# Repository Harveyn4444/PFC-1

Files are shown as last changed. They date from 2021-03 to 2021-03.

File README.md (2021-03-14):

# PFC-1
Hardware and software for the Team Peryton Flight Computer v1

Currently a work in progress

The flight computer is designed around an ATMEGA328 and provides live telemetry and onboard data storage.
GPS, BME280, MPU9250, SGP30, microSD data storage, LoRa comms to a ground-station.

This is designed to fit comfortably in model rockets of 30mm internal diameter.

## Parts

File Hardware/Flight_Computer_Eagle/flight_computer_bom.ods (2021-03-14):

Part | Value | Device | RS / eBay | Units
C1 | 100n | C-EUC0603 | 264-4630 | 25
C3 | 100n | C-EUC0603 | '’
C4 | 100n | C-EUC0603 | '’
C5 | 10u | CPOL-EUSMCA | 538-2278 | 10
C6 | 10u | CPOL-EUSMCA | '’
C20 | 100n | C-EUC0603 | '’
C25 | 100n | C-EUC0603 | '’
D1 | 1A/40V/500mV | BAS40 | in stock
GPS_ANT | U.FL | U.FL
GPS_FIX |  | LEDCHIPLED_0603
J1 |  | JST_2MM_MALE
L1 | 27u | L-EUL1812
LORA_ANT | SMA_EDGE | SMA_EDGE
PROG_HEADER |  | CONN_06FEMALE_LOCK
R1 | 200 | R-EU_R0603
R2 | 10k | R-EU_R0603
R19 | 10k | R-EU_R0603
R20 | 10k | R-EU_R0603
R23 | 1k | R-EU_R0603
R24 | 1k | R-EU_R0603
R25 | 22 | R-EU_R0603
SD | TF-HOLDER | TF-HOLDER
TEST_LED |  | LEDCHIPLED_0603
U$1 | SMD_JUMPER | SMD_JUMPER
U$2 | MPU9250_BB | MPU9250_BB
U$3 | RFM96W | RFM96W
U$4 | 24AA32A | 24AA32A
U$5 | TINY_CELL_GPS | TINY_CELL_GPS
U$6 | NEO-6M_GPS | NEO-6M_GPS
U$7 | BME280 | BME280
U$8 | SGP30_BREAKOUT | SGP30_BREAKOUT
U1 | ATMEGA328P_TQFP | ATMEGA328P_TQFP
U3 |  | V_REG_LM1117SOT223
Y1 | 8MHz | RESONATOR-8MHZSMD_3.2X1.3

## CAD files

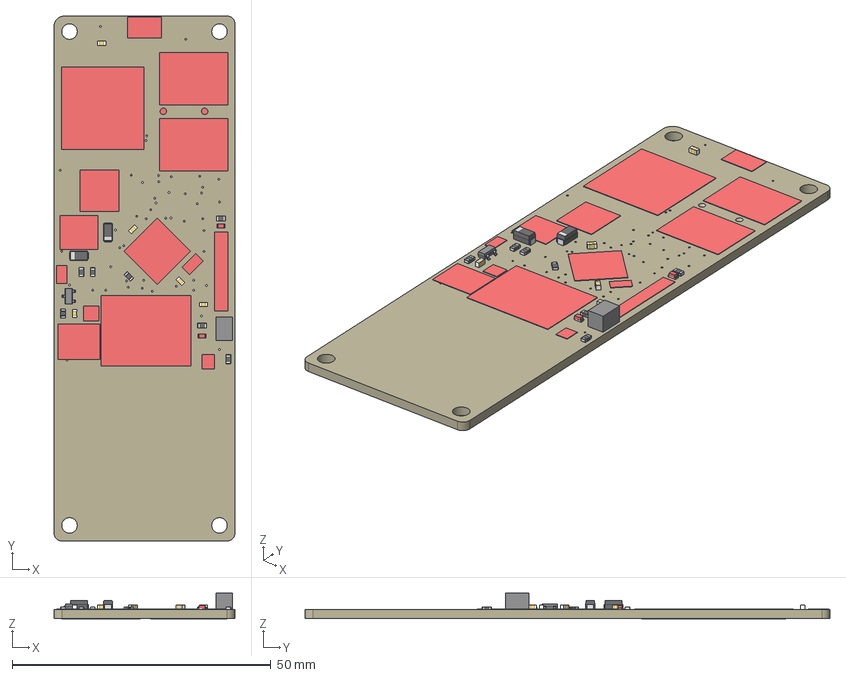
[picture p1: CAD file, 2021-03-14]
Hardware/flight_computer.step
35.0 x 101.5 x 4.97 mm
Board
100n x 5
10u x 2
1A/40V/500mV
CHIPLED_0603 x 2
JST-2-SMD
27u
1X06_FEMALE_LOCK.010
RFM96W
24AA32A
TINY_CELL_GPS
NEO-6M_GPS
SGP30_BREAKOUT x 2
ATMEGA328P_TQFP
SOT223
TF-HOLDER
8MHz
SMD_JUMPER
MPU9250_BB
U.FL
SMA_EDGE

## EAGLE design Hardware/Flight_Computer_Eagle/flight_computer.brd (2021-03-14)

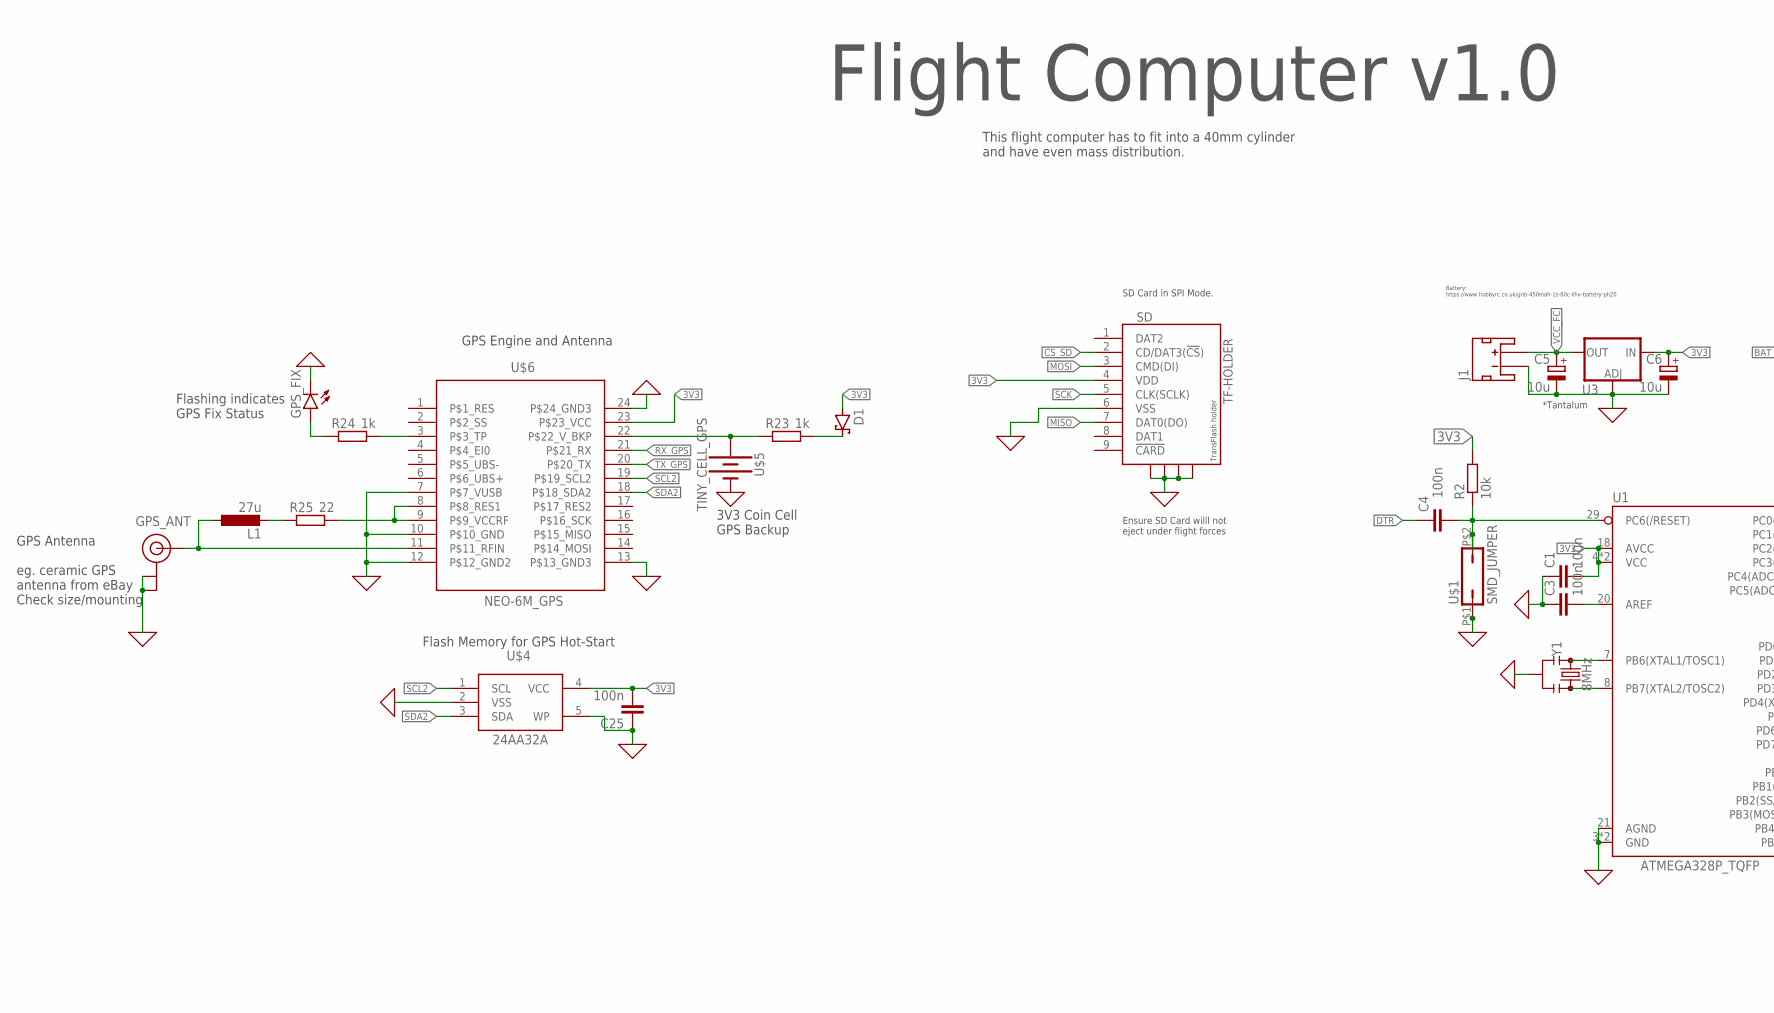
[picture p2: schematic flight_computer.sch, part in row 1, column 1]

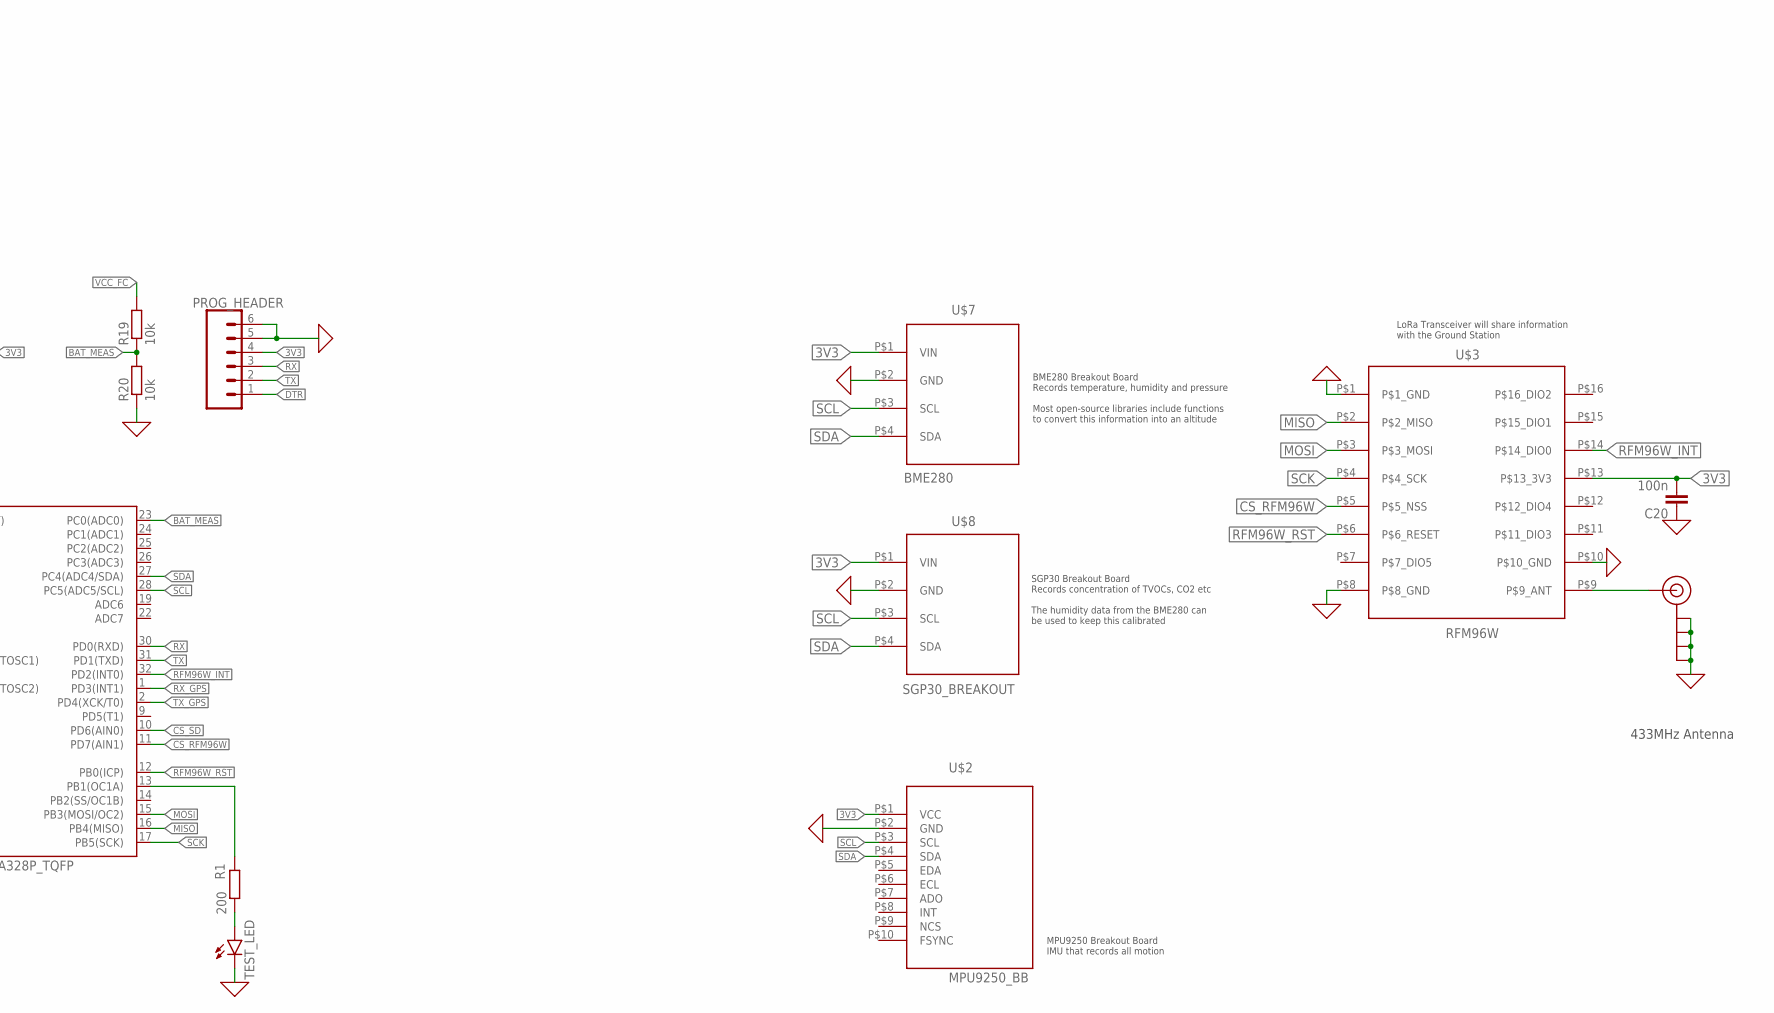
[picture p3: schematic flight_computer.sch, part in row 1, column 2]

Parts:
C1, C3, C4, C20, C25: 100n; C0603
C5, C6: 10u; SMC_A
D1: 1A/40V/500mV; SOT23
GPS_ANT: U.FL
GPS_FIX: LEDCHIPLED_0603; CHIPLED_0603
J1: JST_2MM_MALE; JST-2-SMD
L1: 27u; L1812
LORA_ANT: SMA_EDGE; SMA-EDGE
PROG_HEADER: CONN_06FEMALE_LOCK; 1X06_FEMALE_LOCK.010
R1: 200; R0603
R2, R19, R20: 10k; R0603
R23, R24: 1k; R0603
R25: 22; R0603
SD: TF-HOLDER; TF-PULL
TEST_LED: LEDCHIPLED_0603; CHIPLED_0603
U1: ATMEGA328P_TQFP; TQFP32-08
U3: V_REG_LM1117SOT223; SOT223
U$1: SMD_JUMPER
U$2: MPU9250_BB
U$3: RFM96W
U$4: 24AA32A; SOT23-5L
U$5: TINY_CELL_GPS; TINY_SMD_CELL
U$6: NEO-6M_GPS; NEO-M9N/M8T/M8U
U$7: BME280; BME280_BREAKOUT
U$8: SGP30_BREAKOUT; BME280_BREAKOUT
Y1: 8MHz; RESONATOR-SMD-3.2X1.3

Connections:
0: C1.1, C3.1, C5.-, C6.-, C20.1, C25.1, GPS_ANT.1 (GND), GPS_ANT.2 (GND), GPS_FIX.C, J1.1 (-), LORA_ANT.GND@0 (GND), LORA_ANT.GND@1 (GND), LORA_ANT.GND@2 (GND), LORA_ANT.GND@3 (GND), PROG_HEADER.5, PROG_HEADER.6, R20.1, SD.6 (VSS), SD.S1, SD.S2, SD.S3, SD.S4, TEST_LED.C, U1.3 (GND), U1.5 (GND), U1.21 (AGND), U3.1 (ADJ), U$1.P$1 (1), U$2.P$2 (GND), U$3.P$1 (P$1_GND), U$3.P$8 (P$8_GND), U$3.P$10 (P$10_GND), U$4.2 (VSS), U$4.5 (WP), U$5.P$1 (-), U$6.7 (P$7_VUSB), U$6.10 (P$10_GND), U$6.12 (P$12_GND2), U$6.13 (P$13_GND3), U$6.24 (P$24_GND3), U$7.P$2 (GND), U$8.P$2 (GND), Y1.2
3V3: C1.2, C6.+, C20.2, C25.2, D1.1 (A), PROG_HEADER.4, R2.2, SD.4 (VDD), U1.4 (VCC), U1.6 (VCC), U1.18 (AVCC), U3.3 (IN), U$2.P$1 (VCC), U$3.P$13 (P$13_3V3), U$4.4 (VCC), U$6.23 (P$23_VCC), U$7.P$1 (VIN), U$8.P$1 (VIN)
BAT_MEAS: R19.1, R20.2, U1.23 (PC0(ADC0))
CS_RFM96W: U1.11 (PD7(AIN1)), U$3.P$5 (P$5_NSS)
CS_SD: SD.2 (CD/DAT3(!CS!)), U1.10 (PD6(AIN0))
DTR: C4.1, PROG_HEADER.1
MISO: SD.7 (DAT0(DO)), U1.16 (PB4(MISO)), U$3.P$2 (P$2_MISO)
MOSI: SD.3 (CMD(DI)), U1.15 (PB3(MOSI/OC2)), U$3.P$3 (P$3_MOSI)
unnamed: U1.7 (PB6(XTAL1/TOSC1)), Y1.1
unnamed: U1.8 (PB7(XTAL2/TOSC2)), Y1.3
unnamed: R1.1, U1.13 (PB1(OC1A))
unnamed: R1.2, TEST_LED.A
unnamed: C4.2, R2.1, U1.29 (PC6(/RESET)), U$1.P$2 (2)
unnamed: C3.2, U1.20 (AREF)
unnamed: LORA_ANT.SIG (SIGNAL), U$3.P$9 (P$9_ANT)
unnamed: R23.1, U$5.P$2 (+), U$6.22 (P$22_V_BKP)
unnamed: D1.3 (C), R23.2
unnamed: R24.2, U$6.3 (P$3_TP)
unnamed: GPS_FIX.A, R24.1
unnamed: R25.2, U$6.8 (P$8_RES1), U$6.9 (P$9_VCCRF)
unnamed: GPS_ANT.FEED (SIGNAL), L1.1, U$6.11 (P$11_RFIN)
unnamed: L1.2, R25.1
RFM96W_INT: U1.32 (PD2(INT0)), U$3.P$14 (P$14_DIO0)
RFM96W_RST: U1.12 (PB0(ICP)), U$3.P$6 (P$6_RESET)
RX: PROG_HEADER.3, U1.30 (PD0(RXD))
RX_GPS: U1.1 (PD3(INT1)), U$6.21 (P$21_RX)
SCK: SD.5 (CLK(SCLK)), U1.17 (PB5(SCK)), U$3.P$4 (P$4_SCK)
SCL: U1.28 (PC5(ADC5/SCL)), U$2.P$3 (SCL), U$7.P$3 (SCL), U$8.P$3 (SCL)
SCL2: U$4.1 (SCL), U$6.19 (P$19_SCL2)
SDA: U1.27 (PC4(ADC4/SDA)), U$2.P$4 (SDA), U$7.P$4 (SDA), U$8.P$4 (SDA)
SDA2: U$4.3 (SDA), U$6.18 (P$18_SDA2)
TX: PROG_HEADER.2, U1.31 (PD1(TXD))
TX_GPS: U1.2 (PD4(XCK/T0)), U$6.20 (P$20_TX)
VCC_FC: C5.+, J1.2 (+), R19.2, U3.2 (OUT), U3.4 (OUT)

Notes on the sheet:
*Tantalum
433MHz Antenna
Ensure SD Card willl not eject under flight forces
Flash Memory for GPS Hot-Start
GPS Engine and Antenna
Flashing indicates GPS Fix Status
3V3 Coin Cell GPS Backup
GPS Antenna eg. ceramic GPS antenna from eBay Check size/mounting
Battery: https://www.hobbyrc.co.uk/gnb-450mah-1s-80c-lihv-battery-ph20
SD Card in SPI Mode.
BME280 Breakout Board Records temperature, humidity and pressure Most open-source libraries include functions to convert this information into an altitude
SGP30 Breakout Board Records concentration of TVOCs, CO2 etc The humidity data from the BME280 can be used to keep this calibrated
LoRa Transceiver will share information with the Ground Station
This flight computer has to fit into a 40mm cylinder and have even mass distribution.
Flight Computer v1.0
MPU9250 Breakout Board IMU that records all motion

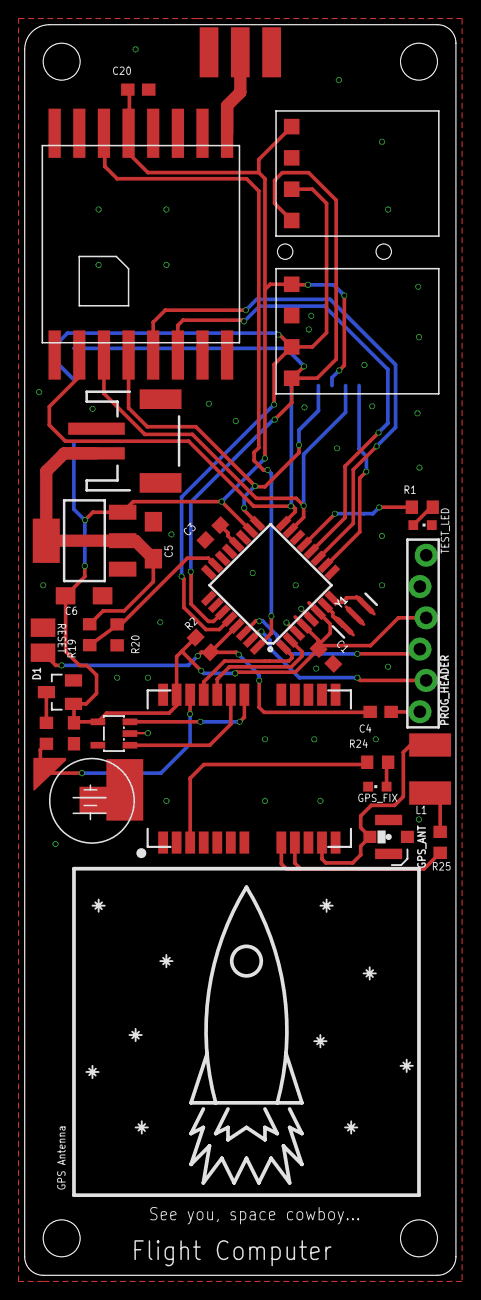
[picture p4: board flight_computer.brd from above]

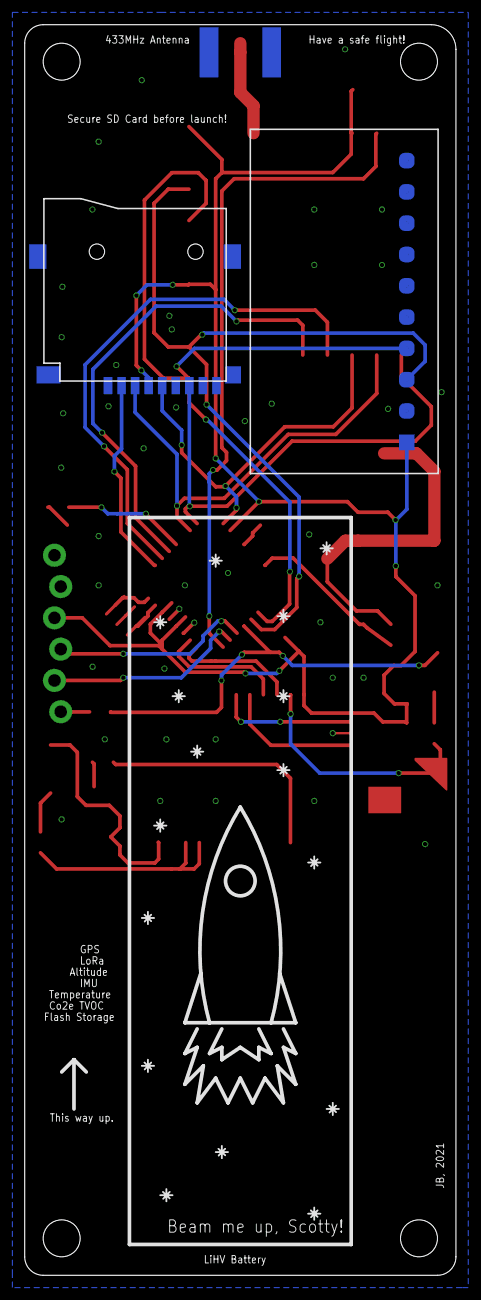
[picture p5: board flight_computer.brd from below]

Board: 2 copper layers, 35.0 x 101.5 mm, 34 parts (2 on the bottom side), 34 nets.

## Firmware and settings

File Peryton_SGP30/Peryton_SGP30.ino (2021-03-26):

#include <Wire.h>
#include "Adafruit_SGP30.h"

Adafruit_SGP30 sgp;

uint32_t getAbsoluteHumidity(float temperature, float humidity) {
    // approximation formula from Sensirion SGP30 Driver Integration chapter 3.15
    const float absoluteHumidity = 216.7f * ((humidity / 100.0f) * 6.112f * exp((17.62f * temperature) / (243.12f + temperature)) / (273.15f + temperature)); // [g/m^3]
    const uint32_t absoluteHumidityScaled = static_cast<uint32_t>(1000.0f * absoluteHumidity); // [mg/m^3]
    return absoluteHumidityScaled;
}

int counter = 0;
float TVOC;
float eCO2;
float H2;
float Ethanol;


void setup() {
 Serial.begin(115200);
 delay(500);
 Serial.println("SGP30 test");

  if (! sgp.begin()){
    Serial.println("Sensor not found");
    while (1);
  }
  //This outputs the sensors chips unique serial number, not too sure if necessary
  Serial.print("Found SGP30 serial #");
  Serial.print(sgp.serialnumber[0], HEX);
  Serial.print(sgp.serialnumber[1], HEX);
  Serial.println(sgp.serialnumber[2], HEX);

   if (! sgp.IAQmeasure()) {
    Serial.println("Measurement failed");
    return;
  }
    if (! sgp.IAQmeasureRaw()) {
    Serial.println("Raw Measurement failed");
    return;
  }
}

void loop() {
//Takes the measurements
TVOC = sgp.TVOC;
eCO2 = sgp.eCO2;
H2 = sgp.rawH2;
Ethanol = sgp.rawEthanol;

 //This warms the sensor up by taking 20 readings which will be indicated as test values
 //These will not be saved
 
 
 for (int counter = 0;counter < 20;counter++) {
  Serial.println("Warming up sensor");
  Serial.print("TVOC "); Serial.print(TVOC); Serial.print(" ppb\t");
  Serial.print("eCO2 "); Serial.print(eCO2); Serial.println(" ppm");
  Serial.print(counter);
  }
if (counter == 20) {
    uint16_t TVOC_base, eCO2_base;
    if (! sgp.getIAQBaseline(&eCO2_base, &TVOC_base)) {
      Serial.println("Failed to get baseline readings");
      return;
    }
    Serial.print("****Baseline values: eCO2: 0x"); Serial.print(eCO2_base, HEX);
    Serial.print(" & TVOC: 0x"); Serial.println(TVOC_base, HEX);
  }

  Serial.print("TVOC "); Serial.print(TVOC); Serial.print(" ppb\t");
  Serial.print("eCO2 "); Serial.print(eCO2); Serial.println(" ppm");
  Serial.print("Raw H2 "); Serial.print(H2); Serial.print(" \t");
  Serial.print("Raw Ethanol "); Serial.print(Ethanol); Serial.println("");


  
delay(500);
}

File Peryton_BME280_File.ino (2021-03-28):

#include <Wire.h>
#include <SD.h>
#include <SPI.h>
#include <Adafruit_Sensor.h>
#include <Adafruit_BME280.h>

#define SEALEVELPRESSURE_HPA (1013.25)

Adafruit_BME280 bme;

File myFile;

float pressure;
float temperature;
float altitude;
float humidity;

void setup() {
  Serial.begin(9600);

  bme.begin();
  if (!bme.begin());
  Serial.println("BME280 - SD Card");

  if (SD.begin(8))
  {
    Serial.println("SD card is present");
  }
  else
  {
    Serial.println("SD card missing or failure");
    while(1);
  }
//Used to clear SD card
/*
  if (SD.exists("BME.txt"))
  {
    Serial.println("Clearing file");
    SD.remove("BME.txt");
    Serial.print("Done");
    Serial.println(" ");
  }
*/
delay(500);
}

void loop() {
temperature = bme.readTemperature();
pressure = bme.readPressure() / 100;
altitude = bme.readAltitude(SEALEVELPRESSURE_HPA);
humidity = bme.readHumidity();


  Serial.print(temperature); Serial.println(" *C");
  Serial.print(pressure); Serial.println("hPa");
  Serial.print(altitude); Serial.println("m");
  Serial.print(humidity); Serial.println("%");

  myFile = SD.open("BME.txt", FILE_WRITE);
  if (myFile)
  {
  myFile.print(temperature); myFile.print(",");
  myFile.print(pressure); myFile.print(",");
  myFile.print(altitude); myFile.print(",");
  myFile.println(humidity);
  myFile.close();
  }
  else 
    {
      Serial.println("error opening BME.txt");
    }

delay(500);

}

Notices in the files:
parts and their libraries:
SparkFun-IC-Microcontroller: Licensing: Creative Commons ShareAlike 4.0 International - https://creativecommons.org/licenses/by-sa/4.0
